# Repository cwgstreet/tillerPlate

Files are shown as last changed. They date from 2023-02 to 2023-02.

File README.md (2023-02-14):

# tillerPlate
-----
FreeCAD model of replacement SmartTrack kayak rudder tiller plate suitable to be water jet cut from stainless steel plate

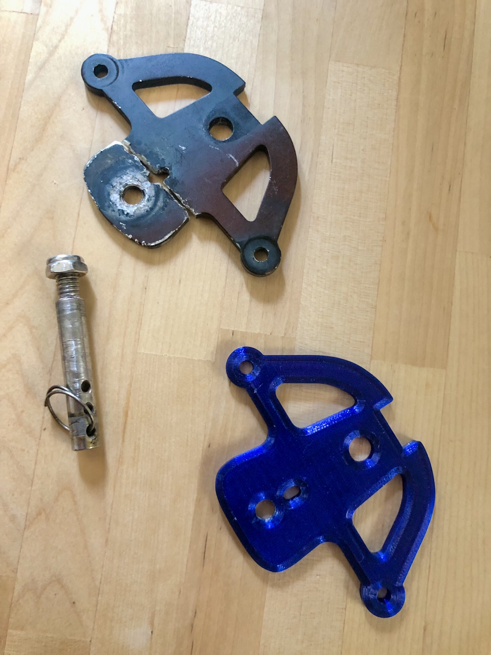
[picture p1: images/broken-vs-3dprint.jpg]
broken tiller plate vs 3D printed part


## Introduction
A buddy of mine has a sea kayak outfitted with a USA-made [Smart Track™ rudder control system](http://www.smart-tracker.com/index.htm) where the aluminium tiller plate has recently broken due to an apparent shear failure.  As he has not been able to source a replacement tiller plate in Australia, I drew up a replacement part in FreeCad and 3D printed a replacement part, mainly to confirm the model.  

## Fabrication

The OEM tiller plate appears to be made of anodised 6061 aluminium.   Although I did all I could to strengthen the 3D printed part used to confirm the model dimensions, clearly a plastic PETG part will be significantly weaker than the OEM part out of 6061 aluminium.

As such, I have provided a drawing file and digital dxf fabrication file that can be given to a metal fabricator to have the part custom water jet or laser cut from a strong, corrosion resistant material such as AISA 304 (marine grade) stainless steel plate.  

Below is a comparison of the material properties of 6061 Aluminium (top bar on bar chart) vs 304 Stainless steel (lower bar on chart).  Clearly 304 stainless steel is much stronger than the OEM prt and less likely to fail again.

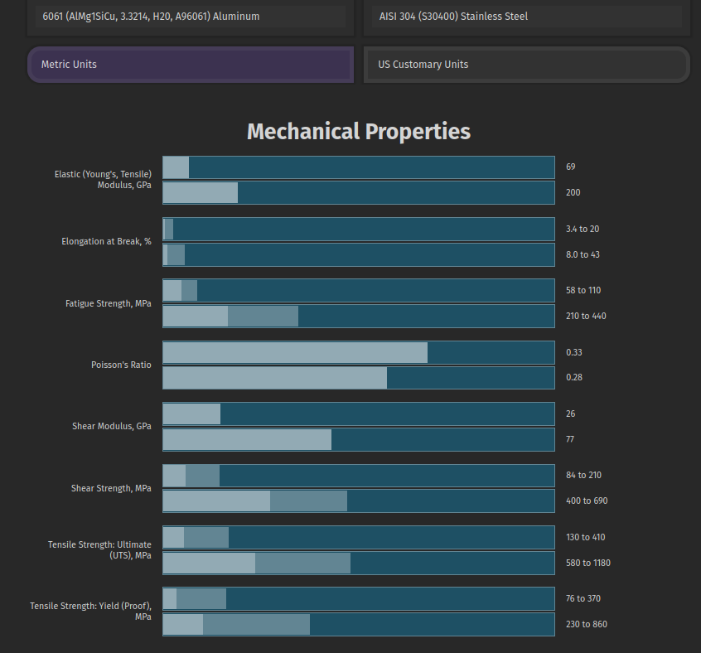
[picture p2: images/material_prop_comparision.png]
6061 aluminium vs 304 stainless steel


### Repository Contents

#### 3D Printing ####
Contains mesh (.stl) file as well as a *.3mf file that has both mesh and slicer settings.  The 3D print setting summary file gives an overview of changes made to optimise the PETG print strength.

#### Dimensions
Contains the few (and incomplete) dimensional drawings that I could find online for the OEM tiller plate

#### Fabrication
This directory contains everything you need to have the part cut out by a metal fabricator: 
*  annotated drawing file,  
*  DXF file containing digital 2D vector cut instructions for water jet or laser cutting, and
*  fabrication instructions.  

Google metal fabricators near you and upload or email these three files to a few fabricators to obtain quotes.

#### FreeCAD models
CAD models made using FreeCAD version 20.2:  the model with threads is intended for 3D printing while the model without threads is for metal fabrication where the threads should be tapped after the part is cut and (tap) holes drilled.

Model was created by importing in a photo image of broken tiller plate and using micrometers to confirm dimensions.  Once, modelled, I 3D printed the part (PETG) so that I could compare it to the broken OEM part and confirm the tiller plate dimensions were correct.

#### Images
Various images of the broken tiller plate, unbroken plate and 3D printed part.

<br>

### Licence

[][cc-by]

This work is licensed under a
[Creative Commons Attribution 4.0 International License][cc-by].

[][cc-by]

[cc-by]: http://creativecommons.org/licenses/by/4.0/
[cc-by-image]: https://i.creativecommons.org/l/by/4.0/88x31.png
[cc-by-shield]: https://img.shields.io/badge/License-CC%20BY%204.0-lightgrey.svg

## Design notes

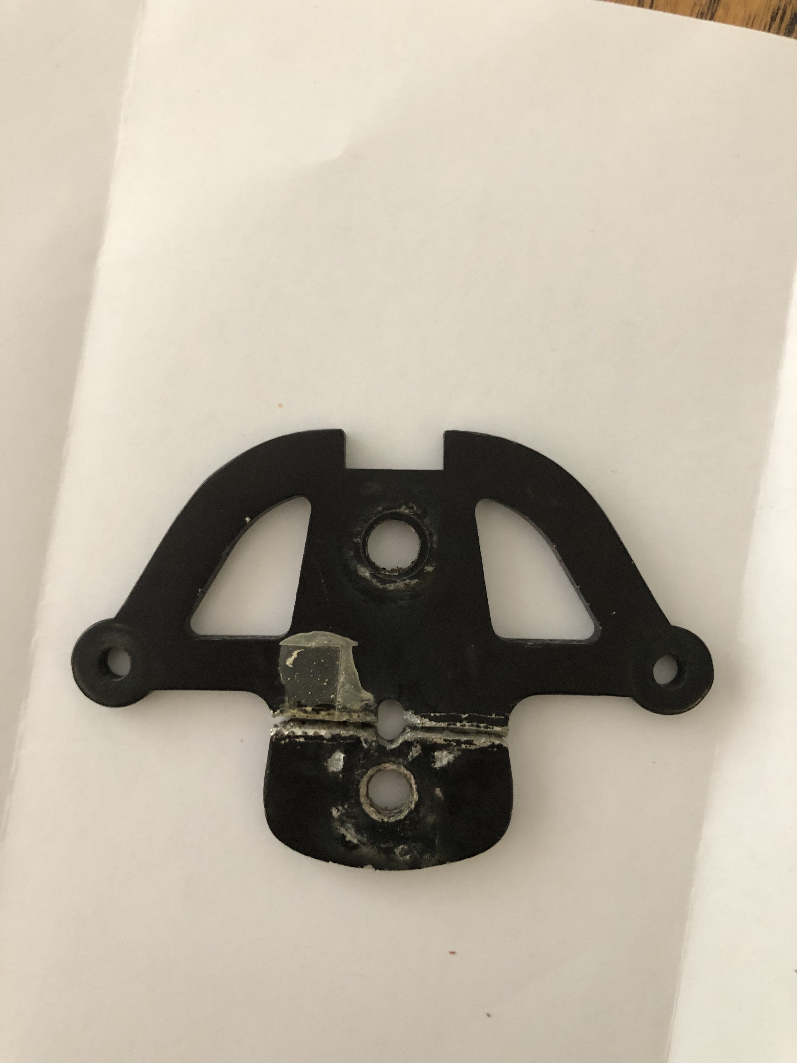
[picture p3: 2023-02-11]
images/broken_kayak_tiller_plate.jpg

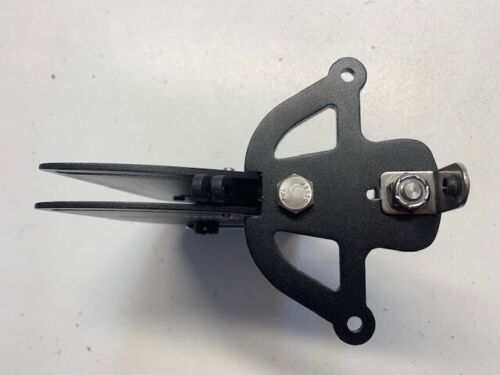
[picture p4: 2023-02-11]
images/smarttrack contol system bracket.jpg

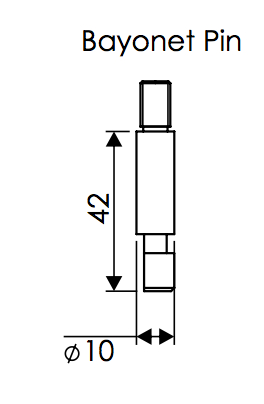
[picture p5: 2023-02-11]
images/Bayonet_Pin.jpg

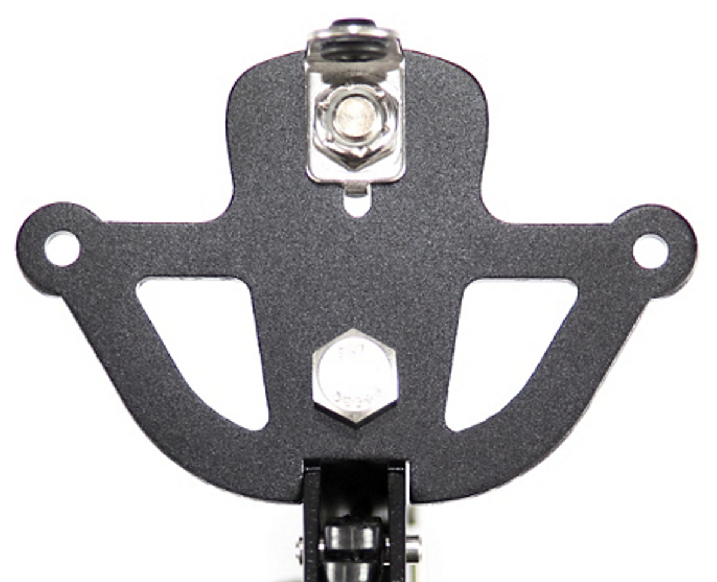
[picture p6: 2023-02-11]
images/tiller plate ad.png

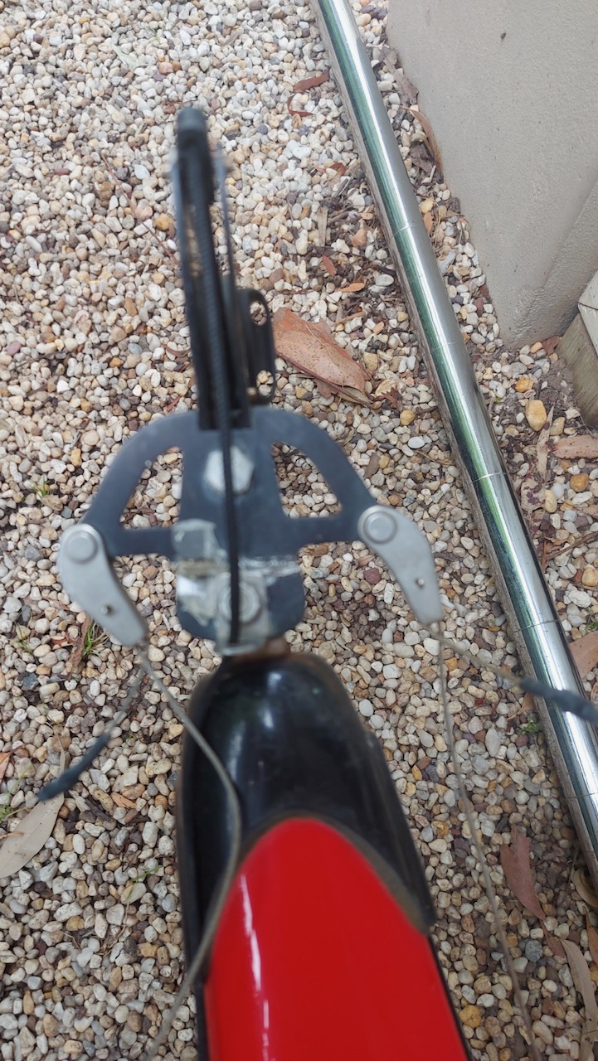
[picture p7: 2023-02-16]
images/kayak-tiller-plate-top.jpeg

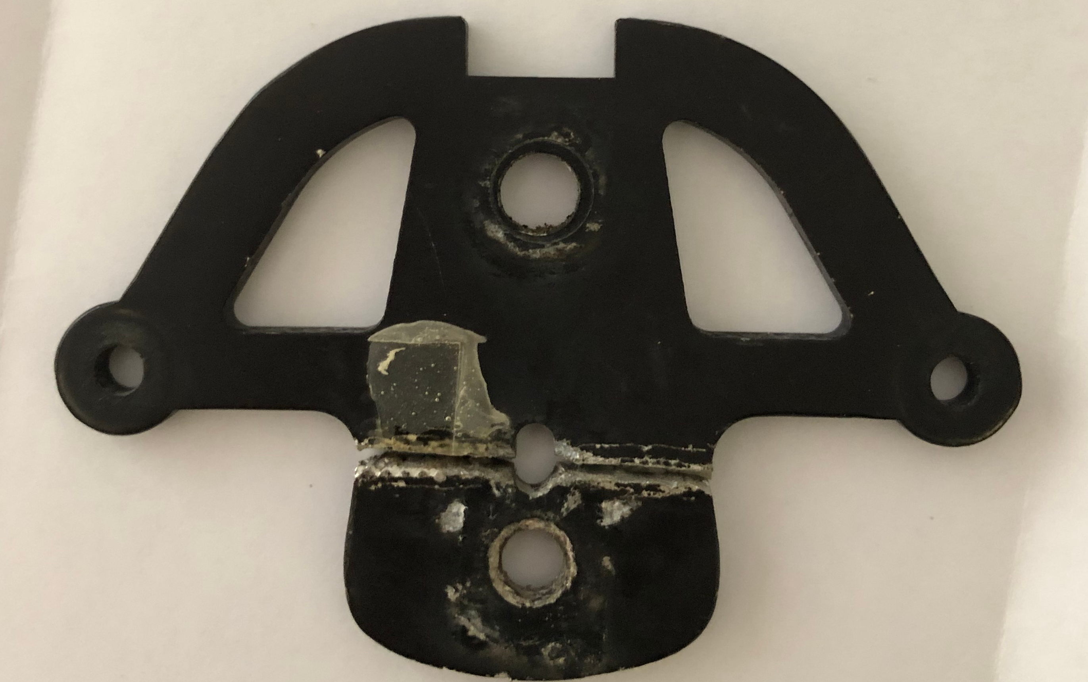
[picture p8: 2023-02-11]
images/kayak tiller plate - broken cropped.jpg

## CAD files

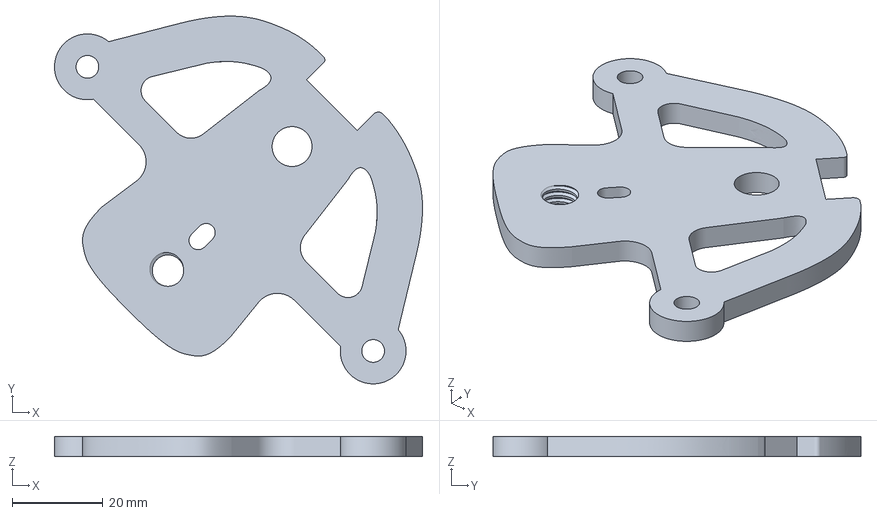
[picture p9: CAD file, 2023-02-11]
3D printing/tillerPlate with 5-16 UNC threads (Meshed).3mf
81.1 x 81.0 x 4.50 mm

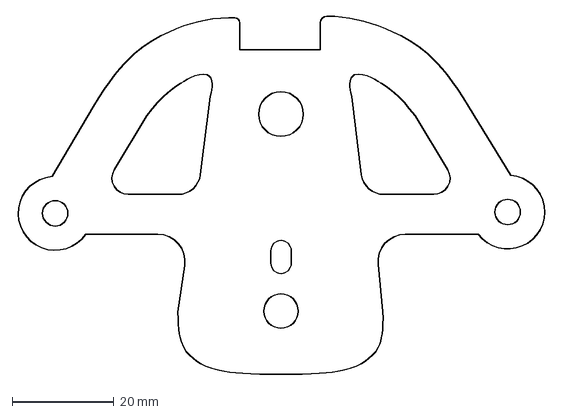
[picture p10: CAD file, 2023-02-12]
fabrication/tiller-plate_Greg-Barbour.dxf
104.1 x 70.4 mm

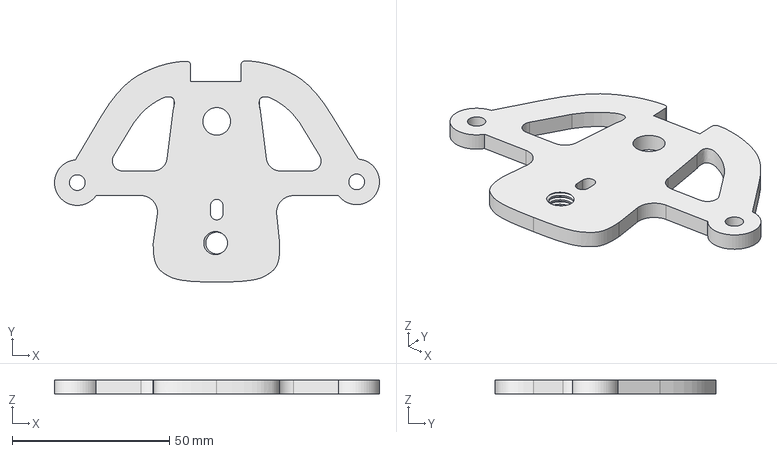
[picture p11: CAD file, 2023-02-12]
freeCad models/tiller-plate-final-drawing.FCStd
103.3 x 70.2 x 4.50 mm

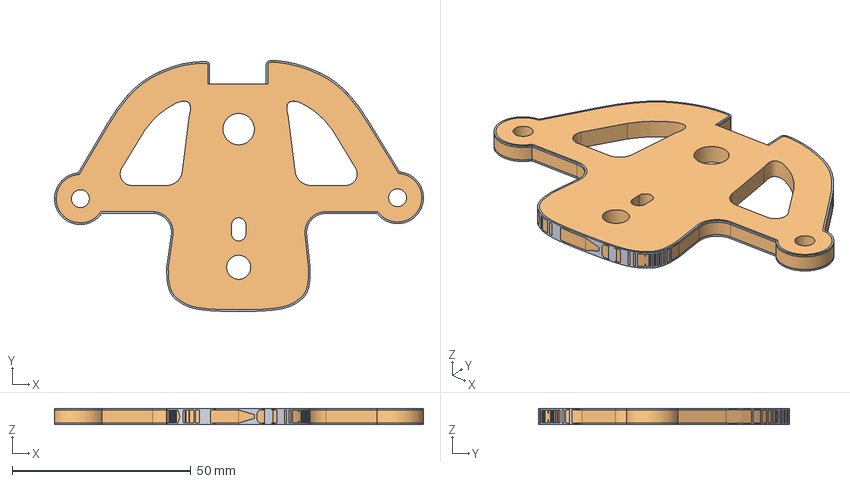
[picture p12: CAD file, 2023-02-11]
freeCad models/tiller-plate-final.FCStd
103.3 x 70.2 x 4.50 mm
Body-tiller-plate

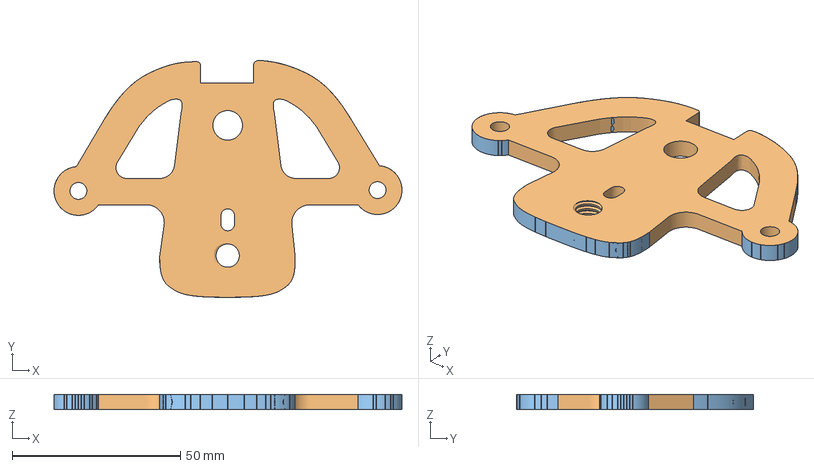
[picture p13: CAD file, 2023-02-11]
freeCad models/tiller-plate-final-threaded.FCStd
103.3 x 70.2 x 4.50 mm
Body-tiller-plate
refined_tillerPlate-with-5/16-UNC-threads
refined_tillerPlate-with-5/16-UNC-threads (Meshed)

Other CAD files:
3D printing/tillerPlate with 5-16 UNC threads (Meshed).stl

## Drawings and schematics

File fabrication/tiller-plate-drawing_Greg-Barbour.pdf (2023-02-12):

103.29

## 5/16 inch UNC threaded hole

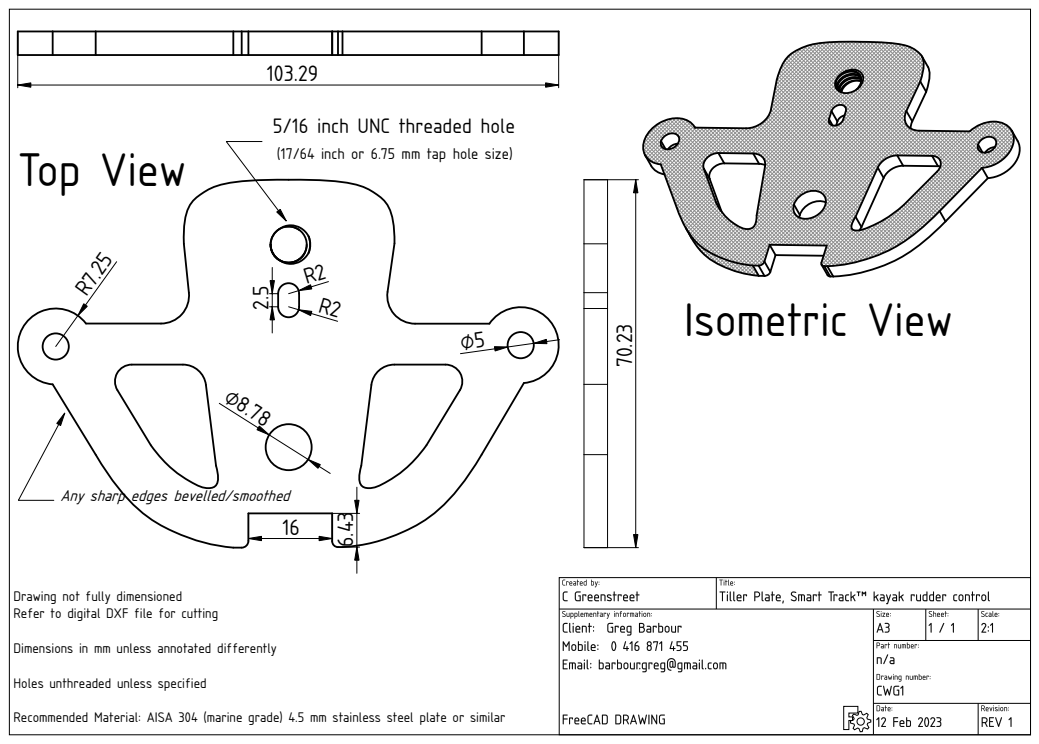
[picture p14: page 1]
Top View; Isometric View

(17/64 inch or 6.75 mm tap hole size)

Any sharp edges bevelled/smoothed

Drawing not fully dimensioned
Refer to digital DXF file for cutting
Dimensions in mm unless annotated differently
Holes unthreaded unless specified
Recommended Material: AISA 304 (marine grade) 4.5 mm stainless steel plate or similar

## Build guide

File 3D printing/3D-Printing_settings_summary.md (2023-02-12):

# 3D Print Settings
---------------

## Summary
The primary purpose of 3D printing the part was simply just to confirm dimensions of the modelled part against the original broken part before having the replacement made by a metal fabricator.

The OEM tiller plate part is made from anodised 6061 aluminium.  As such, any 3D printed part will never be as strong.  Nevertheless, I optimised the 3D print settings and filament choice to improve the 3D part strength.

## Filament
PETG filament was used which should provide some strength improvements over PLA.

## Slicer Settings
The model was sliced with PrusaSliver V2.5 and the following settings were changed to optimised the part strength.

**Print Setting Changes to Prusament PETG profile:**
|Parameter|Setting|default|value used|
|---|---|---|---|
|Vertical Shells|Number perimeters|3|6|
|Horizontal Shells|Solid Layers - Top & Bottom|3|6|
|Infill|Fill density|20%|60%|
|Infill|Fill patter|cubic|gyroid|

## Orientation
Part was rotated 45 degrees on platter in an attempt to minimise stresses along weaker layer orientation planes 

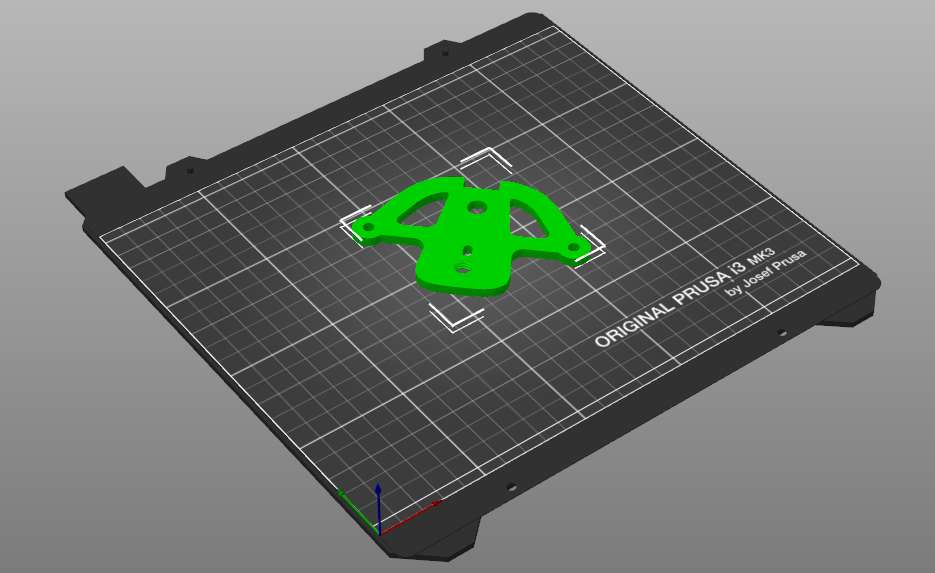
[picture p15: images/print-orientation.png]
45 deg orientation


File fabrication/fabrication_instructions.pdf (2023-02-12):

Tiller Plate Fabrication Instructions

Client: Greg Barbour
Mobile: 0416 871 455
Email: barbour.greg@gmail.com

Suggested Material: 4.5 mm AISA 304 (marine grade) stainless steel plate

Water Jet Cut or Laser Cut using provided DXF file
Tap 5/16 inch UNC threads into the designated hole – refer to technical drawing
bevel / smooth any sharp edges

Any suggestions to reduce cost or improve outcome welcome
Please discuss any proposed changes with me for confirmation prior to fabrication

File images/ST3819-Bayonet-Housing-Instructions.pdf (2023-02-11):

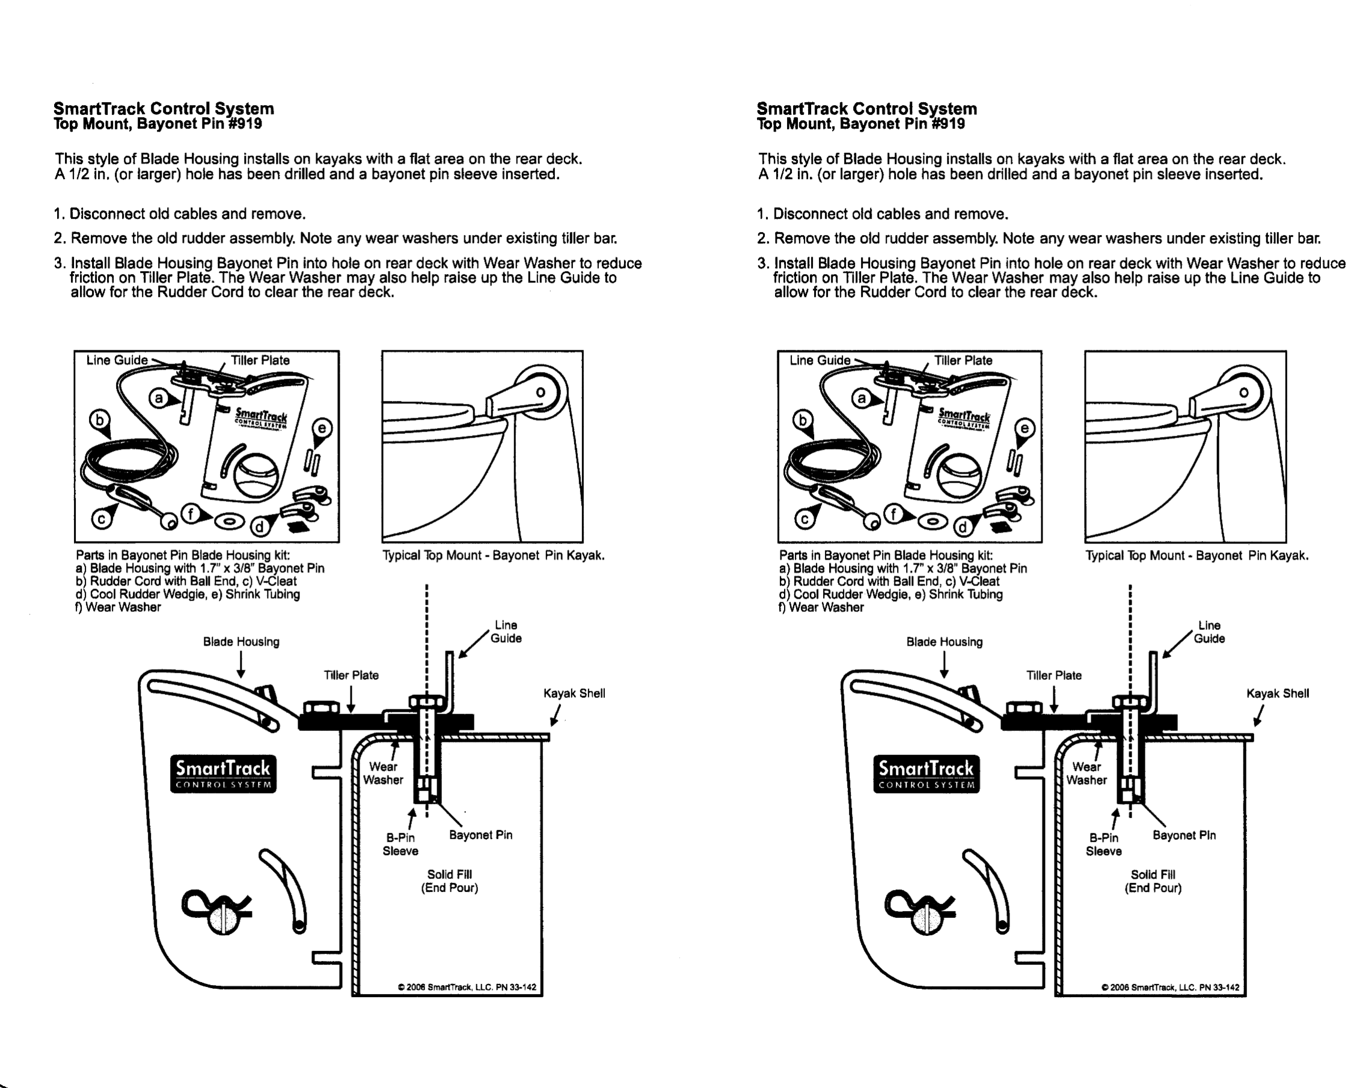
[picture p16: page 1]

# rPate 'Eii= f

# inn:%iF:I::E

tIJEi EIEEFT-TE=EEIE

/ KayakShell

rPlate

# Lii=

Ei

# |HEf%iE:I::E

# tJEi

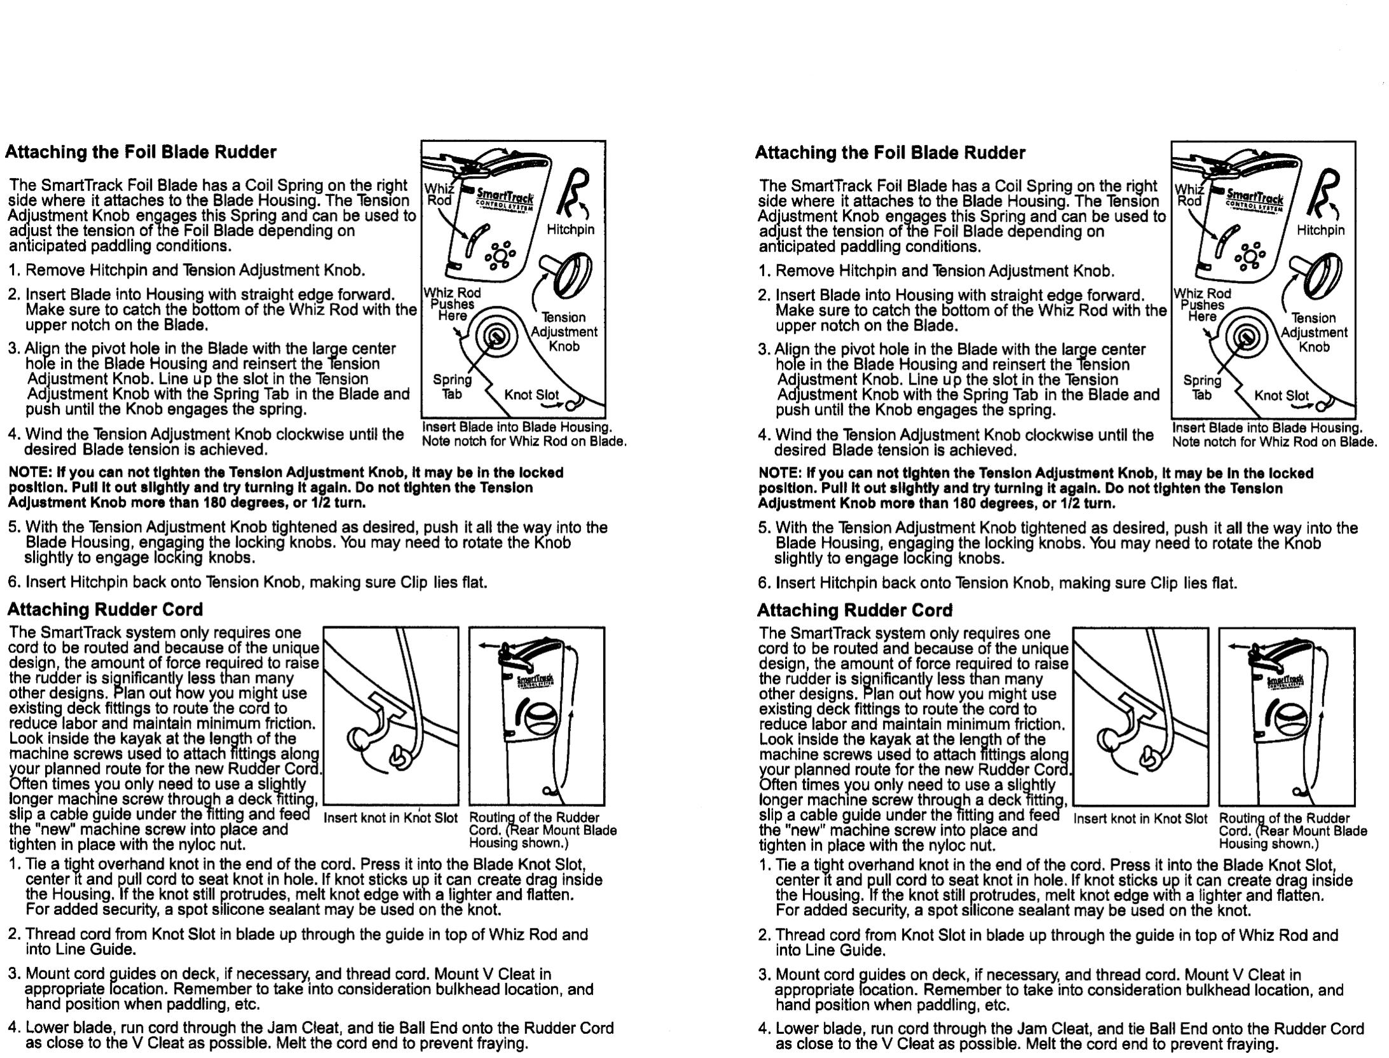
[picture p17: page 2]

g¥ i:: :: =®8E7EI0{§=I;r`es E,fo

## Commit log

2023-02-11 add 3D printing file
    [tillerPlate with 5-16 UNC threads (Meshed).3mf]
2023-02-12 update 3d print setting + image
2023-02-12 create tech drawings
    [tiller-plate-final-drawing.FCStd]
